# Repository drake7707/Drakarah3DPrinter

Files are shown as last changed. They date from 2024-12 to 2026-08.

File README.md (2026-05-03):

# Drakarah 3D Printer
Everything related to my 3D Printer

**[Blog](/blog.md)**

PXL_20260503_095724243_preview

## Info

The printer started of a Formbot kit and has been upgraded.

The printer is capable of printing multiple colors and multiple materials on a 350x350x340 build volume, except for the volume where the docks reside so it's more 350x250x340 and 350x350x100. It also has a cutter toolhead to cut vinyl sheets.

The build steps for the full kit you can find [here](https://github.com/Zev-se/Formbot-voron-2.4-build-guide)

My build log is on Instagram as reels: [part 1](https://www.instagram.com/stories/highlights/18031423286360519/) and [part 2](https://www.instagram.com/stories/highlights/17904237141050138/)

### Hardware Additions:

 - [Clicky clack door](https://github.com/tanaes/whopping_Voron_mods/tree/main/clickyclacky_door) for better sealing of front door
 - [Tough latches](https://www.printables.com/model/1061047-tough-latches-with-space-for-18mm-dowel-pins) (remixed with 1.8mm dowel pins) for easier panel removal
 - [Beefy Z idlers](https://github.com/clee/VoronBFI) for easier Z belt tensioning
 - [Front USB keystone](https://www.printables.com/model/609433-voron-skirt-keystone-for-usbethernet) to easily plug in an USB stick to print from that when network is not availabe
 - Very cheap USB Camera which I dissected to extract the board, access the focus ring and print my own smaller more [adjustable mount](https://github.com/drake7707/Drakarah3DPrinter/blob/main/CAD/CameraMount.step)
 - USB splitter 1 to 4 to give me extra USB connections, one towards the back keystone panel, one towards the front USB keystone, one for the USB camera and one used by a Wifi adapter
 - Sonoff POW R2 to monitor the power usage of the printer (posts to MQTT)
 - [Handles by 1-0-R](https://mods.vorondesign.com/details/xa84lhUN5aMX4nmfZquaQ) with [spacer](https://www.printables.com/model/1098129-top-hat-spacer-for-voron-handle-by-1-0-r) so I can lift and tilt the printer more easily
 - [Wiper nozzle (Bambu style)](https://www.printables.com/model/1054455-voron-24-nozzle-brush-using-bambu-labs-a1-silicon) which is really important as a non clean nozzle will affect probing and thus Z-offset
 - [Stealthchanger](https://github.com/DraftShift/StealthChanger)
    - Top hat to make room for the umbilicals and retain full enclosure
    - Extra Stealthburner toolheads
    - Fysetc Hexa distro fusion board with backpack for CAN distribution
    - Shuttle instead of TAP
    - [Mini BFI](https://github.com/DraftShift/StealthChanger/tree/main/UserMods/BT123/MiniBFI%20%2B%20MicroBFI) so the gantry clears the crossbar
    - [Docks](https://github.com/DraftShift/ModularDock) with crossbar
    - [N3MI exhaust panel v2](https://github.com/DraftShift/CableManagement/tree/main/UserMods/N3MI-DG/Umbilical_plates_V2) and [Fsyetc hexa distro backpack](https://www.printables.com/model/1366367-fysetc-hexa-distro-fusion-backpack) for CAN cable distribution (and USB hub)
    - [Axiscope](https://github.com/nic335/Axiscope) with hartk sexbolt for easy inter-tool nozzle offset calibration
    - 450W Meanwell power supply to replace the Formbot 200W one to make sure all toolheads can be heated at the same time
  - Vinyl cutter toolhead
  - [The Filter](https://www.printables.com/model/334276-the-filter-for-voron-24) with side bed filters (instead of Nevermore) (the screw-in remix)
  - [Filament rollers](https://www.printables.com/model/73636-filament-spool-roller-w-608-bearings)
  - [FilamAtrix toolheads](https://github.com/thunderkeys/FilamATrix) (ECAS inlet, filament runout sensors and filament cutter integration)
  - Replaced the formbot LED bar with [LED bars](https://aliexpress.com/item/1005003166484007.html) that were easily cuttable to size to improve even lighting and remove shadows
  - [CW2 Filament feeders](https://www.printables.com/model/1709031-clockwork2-filament-feeders), with Fly D5 control board in a [backpack](https://www.printables.com/model/1709021-fly-d5-side-backpack) and [Annex belays](https://www.printables.com/model/1709023-annex-belay-array-mount) to keep extruders in sync
    
My steps to convert to StealthChanger are [here](journey-to-stealthchanger.md)

My steps to add a cutter toolhead are [here](journey-to-stealthcutter.md)

### Software additions
 - Using the latest Armbian image instead of the BTT CB1 image as OS because it gets updates and has the latest kernel (was necessary for wifi adapter drivers) and CPU frequency governor support
 - [Klippain Shake&Tune](https://github.com/Frix-x/klippain-shaketune) (for belt comparison and input shaping)
 - [TMC Autotune](https://github.com/andrewmcgr/klipper_tmc_autotune) with everything set to performance because I had issues with 'silent' tuning
 - Exclude object
 - [Klipper Backup](https://klipperbackup.xyz/) (to automatically backup the config to github)
 - [Crowsnest](https://github.com/mainsail-crew/crowsnest) and [Moonraker Timelapse](https://github.com/mainsail-crew/moonraker-timelapse) (for webcam stream and timelapse gneneration)
 - [NanoMQ](https://nanomq.io/) running as a systemd service as a MQTT server, where a Sonoff pow R2 is posting power metrics to, and moonraker ingests those values
 - [udev-media-automount](https://github.com/Ferk/udev-media-automount) as a systemd service to auto mount USB sticks, a symlink is created to the gcodes folder so USB sticks are exposed on the klipperscreen for printing
 - @reboot script to always create a fixed symlink for the usb webcam, it sometimes was /dev/video0, sometimes /dev/video1 so with a udev rule it is now always /dev/webcam
 - Mainsail [fork](https://github.com/fakcior/mainsail/releases) by fakcior for toolchanging and [toolmapping](https://github.com/fakcior/klipper-toolchanger-tool-mapping)
 
## BOM

I try to keep track of a full bill of materials of the entire printer, so anything I add or remove gets updated in the BOM. You can find that [here](BOM.ods)
<details>
  <summary>BOM overview</summary>
  
</details>

## Lessons learned and things I would change if I did a new build

There are some things that I would do different now that I have built one and ran into several issues over the months

 - Print parts out of ABS instead of eSun ABS+. eSun ABS+ used to be recommended but since they changed their formula layer adhesion and heat resistance is bad.
 - Use an Octopus Pro board with a RPI4 instead of a M8P with CB1 that the Formbot came with. Unfortunately there is no option to choose that when ordering a new kit so I'd be stuck with it anyway, but the CB1 really is not powerful enough. A lot of TTCs and timing issues come down to host delays. It can be mitigated somewhat by using the latest kernel with armbian, setting up a performance CPU governor, adding nice to klipperscreen and other non essential processes and so on but all of this would be avoided if I could just use a RPI4. Being stuck with having to use a compute module for the M8P is really limiting the options for upgradability.
 - Get a bigger 24v power supply, the default 200W that came with the kit is good for a single toolhead, but not so if you run multiple toolheads in a toolchanger. I got away with it with using 3 toolheads of varying sized heaters, 70,60 and 40W but there really is no more room to add another one.
 - Use screw in magnets instead of glueing them in with CA glue. They keep popping out. 2 component epoxy also works and it makes it easier to position the magnet properly as it has a longer setting time but ideally I want something that is more robust.
 - Use 3mm wide spring steel instead of 2 1mm piano wires so the umbilicals don't flex to the side as much. I've changed all the umbilicals and it works so much better.
 - Buy decent fans for the toolheads. The cheap ones are either obnoxiously loud or don't cool the hotend that well. Ideally I want fans with rpm monitoring to stop heating when the fan fails.
 - The EBB36 toolhead board is half the price as a SB2209 and works just as well. The terminal block kind of sucks compared to the molex connector for the heater and there is no easy 5V/12V fan option but the price makes up for it. It's also not limited to just the StealthBurner toolhead.
 - Speaking of toolheads, the stealthburner looks good but there are more lightweight and more compact toolheads available. Anthead is popular for StealthChanger builds.
 - Don't buy a Dragon HF hotend. It's really not worth the extra price when you can buy 4 Bambu like TZ2.0 V6 style hotends for the same price. Even the super cheap V6 clones work well.
 - Buy 10m PTFE tube instead of the cheaper 1m, it's so much nicer to just have enough PTFE tube that bends are relaxed. So many issues I had with underextrusion and PLA filament snapping under stress was due to tight bends or pinched points in the bowden tube.
 - Don't put your printer on a spot that has a lot of sunlight. Yes the free heating is nice, but ABS parts really don't like UV and mine significantly bleached after only a couple of months.
 - Anything that is loose will rattle loudly during printing and annoy you. The Filter lids are slide in lids and not tight enough to not rattle, some superglue fixed that. The Clicky clack door panel also needed some extra panel or it would rattle in its extrusions. Test for rattle during assembly.
 - Pull on your dang crimps after crimping. If they come off it was a bad crimp and can cause intermittent connection issues. I've made some bad crimps and the thermistor dipped and caused prints to fail. Having to disassemble to recrimp is no fun, test during assembly.
 - Don't use cheap USB hubs or usb cables that come with boards. The USB A to C cable I used with the hexaboard caused issues, causing very sporadic lost communication issues (or immediate when heating up all toolheads at the same time). I replaced the cable with a USB3.2 branded one that's likely shielded and much thicker and those issues were fixed.

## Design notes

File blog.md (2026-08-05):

# 2026-08-05 CAN bus instability

A couple of months ago I struggled with lost communication. That hasn't happened anymore (touch wood) but I did still see the bytes invalid, bytes retransmit and CAN RX and TX errors creeping up steadily:


After doing all the CAN cable recrimping I thought I finally had solved it but nope. The screenshot above was while T1 was printing, note how T0 gets bytes_invalid from messages to T1. SB2209s are a pain the ass, don't use them in a stealthchanger. With 2 SB2209s I had to put 3 termination resistors in dropping the resistance between CAN L and CAN H to 48ohms instead of the 60ohms it should be, reducing the margin for noise, with just 2 the second SB2209 just refused to connect. It's been a pain in the ass to get the CAN bus working properly with 2 SB2209s and I suspect a lot of the CAN instability comes from having 2. I don't know what CAN transceiver shenanigans it pulls but I have none of that with the EBB36s.

It used to be fine, but as I added more toolheads and the Fly D5 board the CAN bus gets increasingly chatty, increasingly stubby with more reflections and it caused a lot of issues. With just T0 and T1 the CAN bus was far more stable.

I got so fed up with it, a CAN bus that's unstable can ruin a print several hours in, I didn't want to risk long prints anymore. So I bought an EBB36 and replaced the entire T1 toolhead SB2209 and SB0000 board, similar how T2,T3 and T4 work. I had to do several hours of recrimping, extending wires, creating a new umbilical for T1 (it's a microfit connector and not a 2+2 whatever SB2209 uses). Thankfully I still had everything on hand, had spare cabling and wires and 5 hours later I have exactly the same printer in hopefully a better stable CAN state.

And after printing the toolhead cage for T1 on T1 with the new wiring to test the CAN bus and test T1 stability there are 0 errors, 0 bytes invalid, 0 bytes retransmit for an 90 minutes of printing:



So I can finally call this fixed.

# 2026-05-03 Clockwork 2 filament feeders

The long filament path has been annoying me, I had underextrusion issues from time to time, mostly with ABS and I suspected the nearly 2 meters of PTFE tubes to be the cause, mostly because when they were shorter I never had that issue.

So I decided to make filament feeders. There isn't really a specific project or guide for it so I just chose to make some CW2 with a modded ECAS04 at the bottom. Then I bought a very cheap 5 motor control board, a Fly D5 with cheap TMC2209s to control the motors. Finally I also added Annex Belays to make sure the extruders stay synchronized, so one doesn't starve the other of filament or one doesn't push too much filament.

It took a while because I had to make mounts, covers, print everything, solder everything and make compatible connectors for the board but once everything was assembled it works well.

I tried to do proper cable management because that's 20 wires for the motors, 5+1 wires for the filament sensors in the CW2 (I daisy chained the ground) and 5+1 wires for the belay microswitches. It became a mess of cables quickly so I bought some cable shroud and made some cable clips to route it along the extrusion.

PXL_20260503_085024953_preview

PXL_20260503_085055577_preview

PXL_20260503_084830665_preview

PXL_20260502_183926045_preview

PXL_20260502_184737862_preview

# 2026-05-03 Debugging the occasional lost communication

I haven't really used my 3D printer a lot lately, but when I did print something I had the random "Lost communication with the MCU". Tracing the issue proved tricky with just klippy.log so I imported the mcu and CAN bus stats in home assistant to track bytes_invalid and retransmits and CAN errors over time. I also made a standalone [dashboard](https://github.com/drake7707/klipper-comm-tracking) that you can use. That shed some light on things that shouldn't be there, for example T0 and T1 have slowly increasing bytes_invalid and bytes_retransmit. I'm chalking that down to SB2209s shitty CAN transceivers, that refuse to work with a proper CAN bus and require an extra termination resistor. But I also saw increasing CAN TX errors on the hexaboard and considering that's also the USB to CAN board I suspected the board next or the cables leading up to it.

I could luckily (?) reproduce comms issues when I heated all the toolheads at the same time. The hexaboard errors spike and it loses communication immediately. Interestingly when I disabled crowsnest and thus removed the webcam from the equation it worked. This definitely pointed towards USB cabling issues and not the hexaboard itself, the webcam isn't even connected to the hexaboard but to the M8P. I tried using an USB extension cable routed from the front keystone to the hexaboard and it got way worse, those were cheap usb cable extenders for mice/keyboards so no surprise there.

I luckily also had a decent USB3.2 A to C cable I bought as a spare and it's much thicker while shorter than the cable I used for the hexaboard. I replaced it and things worked fine with the webcam still enabled, no more increasing hexaboard TX errors either. The cable tip is molded bigger so I tried using a 90° USB C to C adapter and that immediately caused the issues to come back. So what I think is happening is that the USB C connector of the hexaboard has too much play with cheaper cables. When I jostled the USB cable I saw the hexaboard disconnect so that was likely the culprit. The USB3.2 cable has a better male connector that connects better so I kept that one, redid the back umbilical with that cable, had to pull out the keystone because it was juuuust too short to reach the electronics bay but hey whatever.

So moral of the story: don't use cheap USB cables, don't use cheap USB hubs, they will work but they will also cause intermittent issues that's not a problem for most devices but for time critical elements it is better not to cheap out. Don't even use the provided USB cables that come with the boards, use known reliable ones and it'll save you a lot of headaches.

I've also bought ferrite chokes but didn't receive them yet. I'll add them to all cables and also all CAN cables to hopefully supress noise from motors and other induction sources, to reduce the CAN errors further. Considering the CAN bus is differential I doubt it's going to matter much but if it drops the noise floor it should help.

While I was in the e-bay (I really did not look forward to flipping the ever increasingly heavy and tall printer) I also cleaned up some wire mess and added an extra fan. I'm running the 24v 6020 fans on 12v and always on at 50% while the printer is on and 100% while the printer is active. Idle they are barely hearable and it keeps airflow going over the CB1 and M8P, which is important because the CB1 comes very close to thermal throttling if fans aren't running + the 450W PSU starts its own very noisy fan when the temperature gets too warm, now it doesn't with the fans providing some airflow.

# 2025-08-05 Finishing up & toolless homing

I've finished building the remaining toolhead and routing all the umbilicals and bowden tubes properly. Even put some numbers on the toolheads and filament inlets to keep track of which one is which

PXL_20250804_173238952_preview

The bowden tubes are slightly less than 2m long, which I hope isn't going to introduce too much friction but it does look a lot nicer and has a lot less bends in it.

PXL_20250727_120601292_preview



I've also spent some time getting toolless homing to work. It looks a lot nicer when all the tools are parked in their docks but the toolchanger software didn't allow for shuttle only homing

Watch the video (https://youtube.com/shorts/G2TRkZCBAtQ)

I had to do a couple of things: 

1. Make a Z-endstop that the shuttle could reach but doesn't interfere when tools are on the shuttle PXL_20250803_063140733_preview

2. Define a [tool_probe] with a negative tool number for the endstop
   
2. Make a small patch in klipper-toolchanger to allow multiple probes not triggered if one of the probes is from a negative probe (because the endstop will always be not triggered)

3. Adjust the homing sequence to check if there is a tool or not and home X,Y then move to the endstop and home Z for shuttle only.

It works fairly well and I can pick up tools without an issue.

# 2025-07-26 Summer upgrades

With the Aliexpress summer sales I bought enough stuff to build a 4th and 5th toolhead. This time around I wanted to build the 4th toolhead as a [FilamAtrix](https://github.com/thunderkeys/FilamATrix) toolhead with cutter and runout sensor built in. 

PXL_20250717_131254119_preview

This ended up not being so straightforward. The v6 mount is not supported by FilamAtrix, so I used the one from Filametrix, but that also meant I had to cut the blade differently (I could not cut the hardened steel blade, instead I bent until it shattered in roughly the correct spot) so it rests on the lip of the heat sink and I had to add a sleeve with PTFE tube and a chamfer cut with an exacto knife. That seemed to work alright. I also had to chafe off part of the extruder housing because the clone V6's stick out 1 mm and it clamped the knife down when assembled so cutting away some plastic gave it some room to cut without any friction.

PXL_20250726_083201591_preview

The filament runout sensors also were not easy to install. The ball bearings are exactly 5.5mm so that wasn't the problem, but the holes in the switches did not line up with the holes to mount them. If I did force screws through they would be too close and be always triggered. I ended up fiddling with it, adding some tape to the front, drilling out a hole on the other so I could get it to the position where it reliably triggered/not triggered when I added/removed filament.

I found the best way was to add some layers of tape on the switch and then screw in the self tapping screws with an angle, that seemed to work very consistently across multiple toolheads.

Another issue I had was I had to add spacers for the Octotap as the extruder motor is a lot taller than the ones I bought previously

PXL_20250719_090806072_preview

It still triggers correctly so not a big deal.

I forgot how long it took to trim wires to length and crimp connectors, but in the end I have a new toolhead.

PXL_20250719_121814919_preview

One of the other things I wanted to tackle at the same time was redoing my umbilicals with spring steel. I used piano wire before and they were very sloppy. So I printed the umbilicals v2 exhaust plate from N3mi, detached everything, removed all the cables, and rebuilt the umbilicals, this time with proper PG7 glands on T0 and T1 too so they screwed in snugly, the ones I had from Formbot had a different pitch or out of spec tolerances and it just didn't sit well in the exhaust plate, that also caused a lot of sloppiness.

PXL_20250723_124743320_preview

Pretty happy with that, they look a lot better and hold their form a lot better.

I also managed to snag a Fsyetc Hexa Distro Fusion board for an early bird deal, it's a distribution board for both CAN and USB toolheads but also has a dedicated chip with lots of GPIO. That means I can add a lot more sensors directly to that board instead of having to route everything to the electronics bay.

PXL_20250724_132922123_preview

It's a very new board and there isn't a proper mount for it yet, so I took the time to redesign a new backpack to hold it in place.

PXL_20250726_152013076_preview

One of the other issues I had was filament breaking in the bowden tubes at certain points because the filament was under stress, especially the cheap PLA is very prone to that, so I really want to reroute the bowden tubes to have as little sharp bends as possible, I bought 10m so I can cut them to length and use 2m instead of 1m to make a gentle path towards the spools.

It's still a work in progress in the end the printer will be a lot better, it's the small things.

# 2025-07-10 Sun exposure

I put my printer in my office room on a spot that received a lot of sunlight. I thought the free heating for the chamber would be nice, but now that it's summer the UV is a lot higher and my ABS parts are suffering, I didn't realize how much they have become bleached until I printed a new part and held it next to an older part.

PXL_20250710_134234707_preview

Yikes. Needless to say I moved some things around.

# 2025-06-29 Axiscope

After the last recalibration I ordered the parts to try out Axiscope, basically aligning the tool nozzles visually with a camera. It was pretty cheap anyway, cheaper than a sexball probe and it works great. I had to solder 4 leds (I ordered leds that were too large so I had to drill the holes bigger) to the board, snapped it shut, glued in 2 magnets (4 really seemed overkill with N52) and it works well. The webpage to control the toolhead and measure the offset is pretty easy to use and I could do an entire calibration in a few minutes or less, much faster than the shenanigans I had with the sexball probe and probe that used a StealthChanger pin and bushing, no more going out of bounds, no more samples exceed tolerance, just align and bam done. My calibration was pretty spot on, they were already pretty well aligned, which meant that the values I got from the probe were not very accurate because that suggested over a mm change.

Pretty happy with it, now I just need to change the sexball probe into a normal Z-endstop and set up Axiscope to use the probe for calibrating the Z-offsets.

PXL_20250629_163239899_preview

If you're unsure which tool calibration method to use, I heartily recommend this one.

Another thing I learned recently thanks to https://youtu.be/mkgGAVH_XZM is why my sexball probe and pin probe were so inaccurate no matter what I tried. I thought it was the tolerance of the pin and bushing but I never considered the concentricity of the nozzle orifice. I run very cheap nozzles so I doubt they are symmetrical and concentric at all, giving me a bias towards one side. Another reason why camera based alignment is so much better and easier, it takes out the guessing game of whether tolerances are good enough and doesn't rely on the quality of parts.

# 2025-06-10 Recalibration & print

I managed to recalibrate the nozzles, my sexball probe is useless, it was way off, there's just too much play in the sexball probe shaft and bushing so I need to find a better way for calibration, I might try [Axiscope](https://github.com/nic335/Axiscope), which would be great for X,Y alignment and rather cheap. Z I can do easily with a test print. Anyway, after multiple test prints I got it dialed in properly.

So I did a stress test print and the second attempt worked fine (I had some issues with my config of Tool mapping that nuked the first attempt):



It came out nicely, I scaled up Calidragon by 200% so it was 352 tool changes and it worked flawlessly. It took 4h23min, mostly because my tool changes weren't super optimized to be fast.

So I did that next, increased the Z speed to 200mm/s from 150mm/s, increased Z acceleration to 750mm/s² from 350mm/s². Optimized the pickup and dropoff gcode to use faster XY speeds (300mm/s), removed the M400 from the dropoff gcode that introduced a delay and removed the verify code on pickup as it gets verified after the pickup code runs anyway, it was there to bail out early before potentially dragging the tool off the dock. Bit of a risk but my tools have survived the dive to the bed before.

And i've gotten it down to about 8 seconds for a tool change, it used to be around 15 seconds:

Watch the video (https://youtu.be/LBZMbHjzhpM)

It's really nice to see such a big improvement over my past multi color prints.

# 2025-06-08 Software updates and shenanigans

I was still on the klipper-toolchanger commit from July 2024 and some improvements had been done recently to not have those false positive crash detection triggers anymore, I couldn't also update Klipper because the old version wouldn't be compatible so I took the plunge and updated everything.

Unfortunately a lot had changed since in the gcode as well and nothing was documented, so I had to compare my gcode for picking up and dropping off tools with the newer version. Eventually I got it working, mostly.

One issue I encountered was that the now split dropoff and pickup path was not correct for my Stealthchanger and Stealthburner tool heads, so I used the old path. That worked but not before ramming T0 at full speed into the bottom of the docks.

This has unfortunately some consequences, or maybe it had to do with the update, I don't know, but T0 and T1 would not dock properly anymore. I had to recalibrate the dock and park position of the tools so it drops it nicely without moving and can pick it up without any jerkiness to the pins. This is really important because it would lead to sporadic docking/undocking issues.

After that I noticed when starting a print that the crash protection now works differently and I had to put it a verify tool check in the after later gcode. I don't like this, this causes a delay on every layer change, so I will probably remove that check. Most if not all crashes happen during tool changing anyway.

When I finally gotten a multi tool test  print done again I noticed my calibration was way waaay off, especially on T1. I did remove the nozzle and hotend at some point after a jam and didn't recalibrate.

So I recalibrated, and then the magnet in the shuttle decided to come loose, as well with several pins from T0 due to the added friction of not having a magnet snap the tool in place. Sigh, this would have been a good time to use the two component epoxy I borrowed but apparently lost when I forgot to close the zipper of my bag. I ordered some from Amazon to replace that, but that meant I had to use super glue *again*, which means it will fail again in the near future.

Getting the stupid magnet to sit flush in the shuttle is a pain when there's superflue underneath it. I seemed to have raised it a wee bit because T0 now had inconsistent probe trigger issues. It really never stops does it? Anyway, it was only T0, the others were fine, I loosened the Octotap, pushed it down as far as I could and tightened it again and that did the trick. I already did that on the other tools so I knew it was a good thing to try.

So now I just have to calibrate the z-offset and gcode offset of every tool again, the new magnet location will have shifted things somewhat and then it should be good to go.

I really want to do another multicolor print in a hopefully more reliable fashion but this ended up being a whole lot more work than I planned for.

# 2025-05-15 Some small updates

I've done some small software updates, mainly for some quality of life:

1. I've switched mainsail to the [fork](https://github.com/fakcior/mainsail) with toolchanger support by fakcior. This gives me a nice UI box per tool to activate,load and unload the filament. I could already do that on KlipperScreen but it's still kind of a hassle. Tool remapping is another big one, there is currently no way in OrcaSlicer to swap colors in a painted m3f model, which means I would need to swap the filaments to the tools according to the painted scheme. That's kind of dumb, luckily [this](https://github.com/fakcior/klipper-toolchanger-tool-mapping) allows for remapping the gcode before starting the print. It's still an extra step but at least it's possible now
431562327-bf8e2c3a-cb0d-4ef9-af06-b4f71f41f3fb (*screenshot from the repo*)

2. I've changed some macro's here and there, nothing major, things like not disabling the motors on print end and moving to the nozzle brush before heating up to target temp so the ooze doesn't get dragged all over the bed.

3. The filament rollers work pretty well, but sometimes it does snag hard enough on the roll that it yanks it off the roller sideways, I have added some filament guides to hopefully mitigate that

# 2025-05-06 Vinyl stickers are cool



I used the cutter to make some decals for the top hat, the small lettering was a pain in the ass to transfer but I got it in the end, kinda.

# 2025-05-06 Filament spools driving me crazy

The stealthchanger backpack I made really did not have great routing of the PTFE tubes, my printer is in the corner of my room and accessing the filament spools on the far side was a nightmare, I actually bent the PTFE tube multiple times, there was also no strain relief. The shitty Sunlu PLA+ filament breaks if there is so much as a tiny bit of resistance if it's not dried which also prompted this change.

I got so pissed off I changed the whole thing, initially I designed a spacer to hold the PFTE connectors but that didn't work because the bent upwards would be too great, so option B, drill holes in the backplate of the backpack and use raw force to thread the connectors in. It's not pretty and I really should reprint the back plate with proper m10 threaded holes, but it will do for now.



It makes removing the back plate harder and putting it back in place against the barbs of the connectors even more so (luckily I can push the black rings around it down to keep the barbs from biting into the PFTE tube, one at a time)



Next, filament rollers:

I used [this](https://www.printables.com/model/73636-filament-spool-roller-w-608-bearings) model, bought some 608 bearings, realized I needed 20 not 10, so I printed [some 608 bearings](https://www.printables.com/model/561588-bearings-print-in-place-with-real-rolling-elements), they have more resistance but they work.

I extended the rail to the full size of the top, and then cut it in the slicer with a dovetail cut, that didn't work on such a tiny surface, should have just made a slot on one end and screwed it down, but some electrical tape holds it together.

I designed a [clamp](https://www.printables.com/model/1287401-filament-spool-holder-rail-clamp) to bolt the rail to the side extrusions, similar to the top panel clamps, which makes it sit snugly against the top panel. Together with the weight of all the rollers there is almost no play in the rail.



# 2025-05-04 Cleaning up the rat's nest of wires

One thing that was on my TODO list and I was very reluctant to do was to move the Sonoff Pow R2 from an external extension cord to internal. I was reluctant to because I don't like messing with AC wires, but I finally did it anyway. I quadruple checked all the crimps, using the different crimp clamps on my crimper to make sure the wires are in securely (some weren't so good thing I checked!), then cut some wiring and went to work. Finally I stuck the Sonoff on the bottom plate with some double sided tape.



Everything still works, nothing blew up and it's a lot cleaner behind my printer now.

# 2025-04-28 Cutting edge technology

I finally got a cutter, details are [here](/journey-to-stealthcutter.md)

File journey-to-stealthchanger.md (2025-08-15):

# Journey to stealthchanger

## What

[Stealthchanger](https://github.com/DraftShift/StealthChanger) is a toolchanger so multiple tools can be used in the printer. This is significantly faster than multimaterial that uses filament retract and spool rewinds to feed in new filament.

It requires a fairly large amount of modifications (with multiple options) so I thought it'd be nice to write down the ones I did and what my experience was with them.

## Why

It looks cool and it gives me a spare toolhead. I already had a V6 nozzle that I didn't use that came with the kit because I bought the Dragon HF hotend. Being able to print multiple colors way faster than a filament respooler such as ERCF or Box Turtle + having a lot less waste (some colors such as black -> pink really bleed badly into each other needing a lot of purged filament) was a nice bonus. 

## Step by step

### 1. Second toolhead

Building a new toolhead is pretty much the same as building the first toolhead. This time I had to crimp the wires myself instead of using the provided wire loom but it was pretty straight forward. I stuck with what I already knew and bought a SB2209 (RP2040) CAN board with the same MOONS NEMA 14 extruder).
.

I did buy some shitty fans mostly because I wanted to keep costs down and I didn't know if it would work well. I probably will upgrade to better fans later.

### 2. Docks

I printed and assembled the modular docks from DraftShift Design (the same team behind StealthChanger). Assembling them is pretty straight forward, building the cup filled with RTV silicone was the most annoying and messy part. The wiper to hold the small PTFE tube kept breaking too, but with some superglue and some old laptop screws I managed to get it built.





When mounting them from the top frame it was pretty evident that it wasn't very stable. With the filament I used they vibrated and flexed around a lot, even with torsion so they weren't fully straight. Trying to fix that with the bolts did not work well, so I ended up adding a crossbar.

There are a couple of options to provide bottom support, a crossbar with a doorbuffer is the easiest, it spaces out the support in front of the frame providing clearance for the gantry idlers. I instead already bought some 2020 extrusions for the top hat to size, so I used a crossbar between the vertical frame. That also meant ripping out the default front idlers and replacing them with [Mini BFI](https://github.com/DraftShift/StealthChanger/tree/main/UserMods/BT123/MiniBFI%20%2B%20MicroBFI) that don't portrude past the frame extrusions



I ended up redoing the docks removing the top support with [Crabby docks](https://www.printables.com/model/994635-stealthchanger-stealthburner-minimal-docks-aka-hap). It looks nicer and doesn't obscure as much


Rather than using magnets to lock the tools in I'm using screws with PTFE tube over them. That secures the tools so much in their docks I can put the whole printer on its side and they will stay put. I tried with 5x2mm magnets but they were not powerful enough to keep the tool in place and it limits the tilt enough that I could reduce the umbilical length, which in turn helped with umbilicals not getting stuck under each other



### 3. Sensorless homing

When installing the shuttle there is no X-endstop like there is on the TAP carriage (because otherwise tools wouldn't be able to be detached), so the easiest option is sensorless for X (I ended up doing sensorless for both X and Y). I followed [this](https://github.com/EricZimmerman/VoronTools/blob/main/Sensorless.md) guide and it worked fairly well. The gotcha that got me was that I had to configure TMC autotune as well, otherwise it would work while calibration but fail during normal operation. And it is quite scary home incorrectly and then have the toolhead slam into the gantry. Make sure you calibrate when the gantry isn't level, it adds extra friction so your threshold isn't triggered too soon. 

After installing the shuttle, the belt ends were hindering X homing (and also replacing the umbilicals with stiffer ones) I had to lower the threshold for Stallguard a bit, or it would trigger prematurely so this might need tweaking in the future.

### 4. Faster Z movement

By default the speed is 15mm/s, that is pretty slow to do a tool change. I gradually upped the speed but could not get past 50mm/s. Thinking it was a hardware issue, I checked all the Z-drives grub screws, checked and tensioned all the motor mounts so there is no slack on the big pulley when the motor is initialized (so no backlash), upgraded to [beefy Z idlers (BZI)](https://github.com/clee/VoronBFI/tree/main) and retensioned the belts, but the problem remained. It turned out to be TMC Autotune that put the Z motors in StealthChop and that doesn't work well with higher speeds. Disabling TMC autotune or setting the tuning to performance fixed the issue and I am now running at 100mm/s without a hitch, probably can push it even faster.

### 5. Shuttle

The TAP carriage needs to be replaced with the StealthChanger shuttle. In fact if you put a backplate on a tool and the shuttle on the X rail then everything will still work with the TAP configuration. I ran this for quite some time, this is how I gradually converted my printer to Stealthchanger without losing the ability to print while doing so.

I struggled here to print the shuttle belt grooves properly, so I ended up using the shuttle keeper spacer to hold the belts in place and then bolt the shuttle to the keeper and the carriage.

Finding N52 magnets seemed to be hard, I found some on amazon but they were 6.7mm diameter instead of 6mm, which meant I had to make changes to the holes where they are inserted. At this point I've gone through several destroyed shuttles and backplates so this got delayed a lot. I ended up buying N52 magnets from Lecktor and those were 6mm.







With the help of the belt keeper I tensioned the belts so I didn't even have to use the idlers tension screws much.

I didn't have any issue mating the shuttle with the backplate, I first installed the bushings in the shuttle and glued them in place. I cracked several shuttles trying to insert the bushings (don't use eSun ABS+ for a shuttle). One shuttle ended up cracking when I bolted it to the carriage, which caused the bushings to have too much play and not trigger the Octotap sensor anymore.

My octotap sensors combined with my printed shuttles are very sensitive to slight deviations in angle, so while I initially just extended the shuttle tip by gluing a piece of filament on top so it triggers octotap more reliably it was really solving a problem whose cause would have other issues as well. So my latest attempt that seems to work well is:

 - Install bushings in shuttle, glue them in place so they can't move around and flex
 - Install magnets in the shuttle. Make sure to fit them in first before adding glue because mine set too quickly and caused one of the magnets to not fully seat *sigh*. Tolerances 🙄
 - Mate with a backplate so the pins are aligned to the bushings, glue the pins in place and let it dry while mated with the shuttle, that ensures they stay aligned
 - Add the magnet in the backplate, make sure of the correct polarity, glue it in place after fitting them first
 - Add and adjust the preload screws of the backplate, first screwing them fully in and then back them out by half or quarter turns each. Too far and the octotap won't trigger anymore, not far enough and there will be too much play. When putting the toolhead on the shuttle there should be absolutely no side to side play (rotation around the Y axis), if there is probe accuracy will suffer. Adjust the preload screws until there is none.

Those N52 magnets are strong, make sure to use enough glue, I didn't at first and they got loose after a while causing probe accuracy issues and eventually tool changes to fail. I also had my nozzles dragging over the print during fast travel moves.

After doing that I have good probe accuracy and no issue with tool changes.

In fact to troubleshoot probe accuracy I now check:
 - Loose screws anywhere? Shuttle screws, backplate screws, octotap screws?
 - Are the magnets still sitting flush? Are they loose in either shuttle or backplate?
 - Is there play in the toolhead? Check preload screws and adjust
 - Is there wiggle room in the bushings or pins of the backplate?
 - Are there any cracks in the shuttle, especially near the top bushings. Again really don't use eSun ABS+, layer adhesion is horrible.
 - Are the bushings still securely glued in place?
 - Check for warpage of the hotend/backplate, shim if necessary so the nozzle is perpendicular to the bed
 (this isn't very straight anymore :|)

Any of these things will cause probe accuracy, z-offset inaccuracies and potential docking issues.

*Update April 2025* After some weeks of printing it becare clear that CA superglue is *not* good enough to keep the magnets in place, I've had several failures of both backplates and shuttle where the magnet popped out and then rode along so it couldn't tool change anymore. I've been recommended to use 2 component epoxy glue to secure them or use [6x3 with 2mm ID screw in magnets with M2 self tapping screws](https://discord.com/channels/1226846451028725821/1226846451594821707/1359884602902052894) to secure them into the plastic.

### 6. Top hat

Umbilicals are probably the most important in a StealthChanger build. They need to push the tools into the docks so they sit straight (and they can be picked up well) and don't get yanked off by the weight of the umbilical. In order to have enough clearance for the umbilicals the Z needs to be extended. With the top panel in place on the frame it's impossible to reach the full Z without squishing the umbilical so the solution is a top hat.

I wanted to keep ABS and ASA as options so keeping the printing enclosed was mandatory.

There are several options, from a printed top hat to using extrusions and polycarbonate panels. For a 350 build it's recommended to have at least 20mm extra in height, which would be a lot of plastic. I switched to a Clicky Clack door earlier so I had the 2 spare 24cm stock doors lying around, so I decided to go with the latter option.

I miscalculated the vertical extrusion length (I ordered 25cm, and received 24cm for some reason), so my vertical height was off to mount the panels in the same way with tough latches as on the frame panels. I created [a spacer](CAD/TopHatSpacer_v2.step) that not only holds the extrusions together but provides extra height so the 24cm panels can sit flush with the bottom.

My extrusions inner diameter are 5mm, while the ones I ordered from the top hat are 6mm. This is annoying as I was planning to use some M5 dowel pins. I ended up designing and printing them instead, [dowelpin](CAD/dowelpin.step), but the top hat extrusions chafe away at them so they are only good for a limited amount of top hat removals before they break.

Another issue I had was that the handles I was using interfere with the top hat panels, I designed and created a [spacer](Voron-1-R-Handle-Spacer.step) for that too. I designed it in such a way that it could be printed standing on its side to provide the best tensile strength.



Not having an extrusion for the front of the top hat (it's used as crossbar) is a bit annoying to have a tight seal, but the weatherseal strip seems to work alright. Unfortunately my panels were not cut to 0.1mm tolerances, like 0.5mm too tall, which is giving me issues to put panel clamps on the top. I've instead added more on the side to increase friction so it stays put.

Unfortunately it didn't do much for keeping the chamber temperature high for ABS printing, I barely get above 40° C and that's with The Filter + side filters (4 blower fans) at full blast.

### 7. Umbilicals and CAN wiring

*Update: I have redone the umbical wiring with spring steel (a lot better than piano wire) as well as routing of the PTFE tubes and used a distribution board with a different backpack, read about it [here](https://github.com/drake7707/Drakarah3DPrinter/blob/main/blog.md#2025-07-26-summer-upgrades). I'll leave the old write up below but be aware it's not up to date anymore.*

For the actual umbilicals I bought some 1mm spring steel piano wire and used 2 of them next to the CAN cable to provide enough rigidity. A 3mm spring steel strip is recommended nowadays but I didn't have that so I tried to mimic it as best as I could. I used some tape to hold them in place and used some sleeving over it. The first umbilical I didn't put the piano wire all the way to the toolhead and I feel that was a mistake, it bent and pushed the toolhead backwards on the dock. When I extended the piano wire all the way to the toolhead (I use PUG instead of PG7) that worked much better for staying in the docks.

One thing I had to make sure was that the natural curl the piano wires wanted to make aligned with the arc that I wanted the umbilical to make, so i had to clamp them down at the toolhead in the PUG in exactly the right orientation and the same at the PG7 gland at the exhaust.

I used the [umbilical exhaust by N3MI](https://github.com/DraftShift/CableManagement/tree/main/UserMods/N3MI-DG/Umbilical_Plates) to attach the exhausts at the back. I had a lot of trouble getting the PG7 glands to screw in. I initially thought I probably need to tune shrinkage and hole compensation settings more but after buying some new PG7 glands those fit perfectly, so the ones I got with the Formbot kit were out of spec.

Determining the length of the umbilical was not that easy. The docks in the corners need a slightly longer one to make the same arc. Mine are about 70cm but I feel that's still too long. It's a lot of testing that the toolhead doesn't get yanked backwards but also that the front corners can be reached without putting too much strain on the umbilical.

After some tweaking 60cm is a better length, with a longer length they often got stuck underneath each other and they tended to flop more to the side, with 60cm they don't interfere with each other anymore even though they pull the tool backwards more but the tilt is limited by having the physical screws on the docks to lock the tools in place. Too much tilt would prevent correct alignment of the backplate pins with the shuttle so those docks screws are very mandatory with a shorter umbilical.



Then I clipped the reverse bowden tube alongside the umbilicals with some custom designed [cable clips](CableClip-Body001.step) (sized to my umbilical thickness)

.

Finally the CAN wiring. Initially I had the CAN cable broken out in the electronics bay and used some wago clips, but that meant I also had to run each umbilical downwards, that's not very scalable with more toolheads, so I moved the wagos up near the exhaust and ran 2 1.5mm² power wires along with some leftover CAN cable for the CAN wires, all sleeved together and then attached the umbilicals there.



I've designed [a box](https://www.printables.com/model/1119606-wago-can-distribution-box-for-n3mi-umbilical-plate) to make it neater.





### 8. Configuration

#### Installation 

So far installation and configuration is pretty straight forward, I already defined toolheads in seperate config files, so following the [guide](https://github.com/DraftShift/StealthChanger/wiki/Configuration) was relatively easy. Make sure to use the [easy config](https://github.com/jwellman80/klipper-toolchanger-easy) by @averen or use the klipper-toolchanger from June 2024 because newer commits have broken stealthchanger. There is a DSD fork in the works that will bring everything together but right now it's still in alpha and I have not used it yet.

#### Calibration

One gotcha I had during [dock position calibration](https://github.com/DraftShift/StealthChanger/wiki/Calibration) was that (as of the time of writing) it's still recommended to home, QGL and home again with T0, and then find the positions of the docks (this is not mentioned in the guide). The moment I took T0 off the shuttle the crash protection triggered disabling the motors so it was impossible to try and pick up a tool manually to find its dock position. Running `STOP_TOOL_PROBE_CRASH_DETECTION` is necessary to prevent this. Also when picking up the other tool manually, before testing the docking path make sure you re-run `INITIALIZE_TOOLCHANGER` because otherwise it will think T0 is still active and will try to dock on T0 instead of the correct dock (as I found out the hard way).

For the cups filled with RTV the spring on one was too weak causing it to not contact the nozzle. I added a few washers so it sits higher and that seemed to help but it tilts the toolhead backwards. I've added some M3x12 screws in the docks that correspond to the holes of the M3x50mm screws of the StealthBurner toolhead to prevent to lock it in place. It still tilts back a bit but it can't because the screws are holding it back further. That seemed to work fine. Normally you would add screws the other way and use 5x2mm magnets to lock it in place, but I don't have magnetic screws at the moment. I set it up in the following order: 1) put the tool on the dock 2) adjust the cup height so the nozzle hits the RTV of the cup but not too much it causes too much tilt 3) adjust the back of the dock so the toolhead sits level and doesn't tilt to one side other than backwards 4) do a manual pick up and release with the shuttle and adjust until the toolhead doesn't stray too far off so the pins still go smoothly into the bushings once you pick it up again.

For the Z-offset I initially set up both toolheads, but T1 z-offset is never used (T0 is the reference for homing and every position is based on that). I copied over the z-offset I had before with TAP changer and it worked straight away.

I used a sexball probe which wasn't straight forward to get working. There is quite some play on the shaft so I questioned the accuracy. I had to increase the sample tolerance setting a lot to have it finish. I also ran out of bounds several times as the probe is at the fringe of where the toolhead can be. I had to move the bed backwards a bit so the sexball probe testing range was within bounds. At the same time I also moved the nozzle wiper to the front because that couldn't be reached anymore. So what was a simple crimp wire, mount to extrusion, done turned out to be more of an ordeal. In the end I ran it several times and used the offsets that occurred the most. After test printing that also seemed to be the correct offset.

#### Slicer setup

I use OrcaSlicer and as of v2.2.0 it supports multiple toolheads. Unfortunately I had to set up a whole new printer profile from the Generic Multitool profile to do so (and re-apply all my settings). I've set the idle temp in the filament settings and preheat time in the ooze prevention settings so it drops the temperature when not in use (saving power and squeezing slightly more margin out of the 200W PSU). To ramp them up to idle at the start I specified those temperaturates along in PRINT_START. Replace M104 with M109 to do them one by one if the PSU is not strong enough.

This is the machine G-Code from OrcaSlicer (credits go to @theaninova on discord):
```
PRINT_START TOOL_TEMP={first_layer_temperature[initial_tool]} {if is_extruder_used[0]}T0_TEMP={first_layer_temperature[0]} T0_IDLE_TEMP={(idle_temperature[0] == 0 ? (first_layer_temperature[0] + standby_temperature_delta) : (idle_temperature[0]))}{endif} {if is_extruder_used[1]}T1_TEMP={first_layer_temperature[1]} T1_IDLE_TEMP={(idle_temperature[1] == 0 ? (first_layer_temperature[1] + standby_temperature_delta) : (idle_temperature[1]))}{endif} {if is_extruder_used[2]}T2_TEMP={first_layer_temperature[2]} T2_IDLE_TEMP={(idle_temperature[2] == 0 ? (first_layer_temperature[2] + standby_temperature_delta) : (idle_temperature[2]))}{endif} {if is_extruder_used[3]}T3_TEMP={first_layer_temperature[3]} T3_IDLE_TEMP={(idle_temperature[3] == 0 ? (first_layer_temperature[3] + standby_temperature_delta) : (idle_temperature[3]))}{endif} {if is_extruder_used[4]}T4_TEMP={first_layer_temperature[4]} T4_IDLE_TEMP={(idle_temperature[4] == 0 ? (first_layer_temperature[4] + standby_temperature_delta) : (idle_temperature[4]))}{endif} {if is_extruder_used[5]}T5_TEMP={first_layer_temperature[5]} T5_IDLE_TEMP={(idle_temperature[5] == 0 ? (first_layer_temperature[5] + standby_temperature_delta) : (idle_temperature[5]))}{endif} BED_TEMP=[first_layer_bed_temperature] TOOL=[initial_tool] CHAMBER_TEMP=[chamber_temperature] FILAMENT=[filament_type]
```

And this is my print start:
```gcode
[gcode_macro PRINT_START]
variable_printing: False
variable_tools_used_during_print: []
gcode:
  {% set material = params.FILAMENT|default('PLA')|string %} ; Get material type from params
  {% set bedtemp = params.BED_TEMP|default('0')|string %} ; Get the bed temperature
  {% set chambertemp = params.CHAMBER_TEMP|default('0')|string %} ; Get the chamber temperature
  
  M117 Initializing  
  SET_GCODE_VARIABLE MACRO=PRINT_START VARIABLE=printing VALUE=False

  # Register the tools used during print
  {% set tools_used_during_print = [] %}
  {% for tool_nr in printer.toolchanger.tool_numbers %}
    {% set tooltemp_param = 'T' ~ tool_nr|string ~ '_TEMP' %}
    {% if tooltemp_param in params %}
      {% set _ = tools_used_during_print.append(tool_nr) %}
      SET_GCODE_VARIABLE macro=PRINT_START variable=tools_used_during_print value="{tools_used_during_print}"
    {% endif %}
  {% endfor %}
  RESPOND TYPE='echo' MSG="The print uses the following tools: {tools_used_during_print|join(' ')}. M104 will be ignored for all other tools while the print is active"

  INITIALIZE_TOOLCHANGER
  CHECK_ACTIVE_T0 ; Check T0 is active
  
  SET_DISPLAY_TEXT MSG="Heating the bed to target temperature"
  M190 S{bedtemp} ; heat the bed

  SET_DISPLAY_TEXT MSG="Heating T0 hotend to 150c" 
  M109 S150 ; heat the nozzle
    
  SET_DISPLAY_TEXT MSG="Homing" 
  STATUS_HOMING
  G28
  
  SET_DISPLAY_TEXT MSG="Cleaning nozzle" 
  STATUS_CLEANING
  CLEAN_NOZZLE

  SET_DISPLAY_TEXT MSG="Quad Gantry Leveling" 
  STATUS_LEVELING
  QUAD_GANTRY_LEVEL

  SET_DISPLAY_TEXT MSG="Homing" 
  STATUS_HOMING
  G28

  SET_DISPLAY_TEXT MSG="Building adaptive bed mesh" 
  STATUS_MESHING
  BED_MESH_CALIBRATE ADAPTIVE=1             ; do a bed mesh
  G1 Z20 F3000                   ; move nozzle away from bed
    
  M109 S0 # Stop to heat, the actual printing may happen with a different hotend.

  SET_DISPLAY_TEXT MSG="Heating up the hotends to idle temp"
  # Preheat all the hotends in use
  {% for tool_nr in printer.toolchanger.tool_numbers %}
    {% set tooltemp_param = 'T' ~ tool_nr|string ~ '_IDLE_TEMP' %}
    {% if tooltemp_param in params %}
      M104 T{tool_nr} S{params[tooltemp_param]}
    {% endif %}
  {% endfor %}

  SET_DISPLAY_TEXT MSG="Switching to active tool" 
  {% if params.TOOL is defined %}
    T{params.TOOL}
  {% endif %}

  SET_DISPLAY_TEXT MSG="Heating hotend to target temp" 
  M109 S{ params.TOOL_TEMP }
  G0 Z2 F300 ;Move up a bit
  G92 E0 ; Zero extruder
  
  START_TOOL_PROBE_CRASH_DETECTION
  SET_GCODE_VARIABLE MACRO=PRINT_START VARIABLE=printing VALUE=True
  
  SET_DISPLAY_TEXT MSG="Cleaning nozzle ooze" 
  STATUS_CLEANING
  CLEAN_NOZZLE ; clean the nozzle to remove and leftover ooze
    
  SET_MATERIAL MATERIAL={material} ; setup the things specific for the material
    
  SET_DISPLAY_TEXT MSG="Printing" 
  STATUS_PRINTING  
  
#####################################
##            Set Material         ##
##      Version 1.0  2023-4-2      ##
#####################################
## From: https://github.com/rootiest/zippy-klipper_config
## Set Material-specific Configs
## 
## Add this immediately after your start_print line of the start gcode in Prusa/SuperSlicer:
##     SET_MATERIAL MATERIAL='{filament_type[initial_extruder]}'
## 
## Add this immediately after your start_print line of the start gcode in Cura:
##     SET_MATERIAL MATERIAL='{material_type}'
## 
[gcode_macro SET_MATERIAL]
description: Set values based on material type
variable_material: ''
gcode:
    {% set material = params.MATERIAL|default('PLA')|string %} ; Get material type from slicer
    {% if material == 'PLA' %} ; If material type is PLA
        SET_FAN_SPEED FAN=nevermore_fan SPEED=0.0
    {% elif material == 'ABS' %} ; If material type is ABS
        SET_FAN_SPEED FAN=nevermore_fan SPEED=1.0
    {% elif material == 'ASA' %} ; If material type is ASA
        SET_FAN_SPEED FAN=nevermore_fan SPEED=1.0
    {%else %} ; If any other material type
        SET_FAN_SPEED FAN=nevermore_fan SPEED=0.0
    {% endif %}
```

I had the pressure advance settings per filament in the SET_MATERIAL, but I moved that to the filament settings in OrcaSlicer because it emits a SET_PRESSURE_ADVANCE at every filament change.

To make sure T0 is active I used the following gcode. Using any other tool to home and QGL is going to cause issues with z-offset and docking:
```
[gcode_macro CHECK_ACTIVE_T0]
gcode:
  {% set tool = printer[printer.toolchanger.tool].tool_number %}
  {% if tool != 0 %}
    {% set msg = 'T0 is not active, active tool is ' ~ tool|string ~ '. Cancelling print.' %}
    SET_DISPLAY_TEXT MSG="{msg}"
    RESPOND TYPE=error MSG="{msg}"
    CANCEL_PRINT
  {% endif %}
```

One issue I had was that it took a long time for the temperature to settle, even with long preheat time it often caused delays at tool swaps. OrcaSlicer emits M109 at every filament change when using ooze prevention, the default M109 waits until it's stable within 0.5 degrees which is too precise.
There is already an override from TAP changer, but this override from DSD is better as it allows you to set the deadband, so rather than a 0.5° it now uses a 3° variance for stability. This still needs to be tweaked depending on the hotend. My Dragon HF stabilizes much quicker than the cheap V6 nozzle.
```

[gcode_macro M109]
rename_existing: M109.1
description: [T<index>] [S<temperature>] [D<Deadband>]
  Set tool temperature and wait.
  T= Tool number [optional]. If this parameter is not provided, the current tool is used.
  S= Target temperature
  D= Dead-band, allows the temperature variance +/- the deadband
variable_default_deadband: 6.0
gcode:
    {% set s = params.S|float %}
    {% set deadband = default_deadband|float %}
    {% if params.D is defined %}
        {% set deadband = params.D|float %}
    {% endif %}
    {% set tn = params.T|default(printer.tool_probe_endstop.active_tool_number)|int %}
    {% set tool = printer.toolchanger.tool_names[tn]|default('') %}
    {% set extruder = printer[tool].extruder %}

    SET_HEATER_TEMPERATURE HEATER={extruder} TARGET={s}
    {% if s > 0 %}
        TEMPERATURE_WAIT SENSOR={extruder} MINIMUM={s-(deadband/2)} MAXIMUM={s+(deadband/2)}   ; Wait for hotend temp (within D degrees)
    {% endif %}
```
#### Workaround for an annoying [bug](https://github.com/SoftFever/OrcaSlicer/issues/7842) in OrcaSlicer 2.2.0

*Note: OrcaSlicer 2.3.0 is out where this is fixed so this is now not necessary anymore*

When printing single color on any toolhead other than T0, it still preheats T0 for some reason, and it does so multiple times so just setting it to 0° does not work for long. I worked around that by keeping track of the tools that are used in PRINT_START (see '#Register the tools used during print' above) and then check if the M104 call to heat a toolhead is in that list:
```gcode
[gcode_macro M104]
rename_existing: M104.1
description: [T<index>] [S<temperature>]
  Set tool temperature.
  T= Tool number, optional. If this parameter is not provided, the current tool is used.
  S= Target temperature
gcode:
  {% if params.T is defined %}

     {% set can_change_temp = False %}
     {% if printer["gcode_macro PRINT_START"].printing %}
      {% set tool_nr = params.T|default(printer.tool_probe_endstop.active_tool_number)|int %}
      {% set tools_used = printer["gcode_macro PRINT_START"].tools_used_during_print %}
      
      {% if tool_nr in tools_used %}
        #RESPOND TYPE=echo MSG="Tool {tool_nr} is used in print, can set temp to requested tool"  
        {% set can_change_temp = True %}
      {% else %}
        RESPOND TYPE=echo MSG="Tool {tool_nr} is not used in print, ignoring request for M104"
      {% endif %}
    {% else %}
      #RESPOND TYPE=echo MSG="Not printing, can set temp to requested tool {tool_nr}"
      {% set can_change_temp = True %}
    {% endif %}

    {% if can_change_temp %}
      {% set newparameters = "" %}
      {% set newparameters = newparameters ~ " T="~params.T %}
      {% if params.S is defined %}
        {% set newparameters = newparameters ~ " TARGET="~params.S %}
      {% endif %}
      SET_TOOL_TEMPERATURE{newparameters}
    {% endif %}
    
  {% else %}
    M104.1 {rawparams}
  {% endif %}
```

### 9. Test print

I created some cubes in Orca, positioned them next to each other, changed their height to 1mm and set each one to a different tool. That allowed me to see if the calculated Z-offset of T1 is good (based off the gcode z offset) and to see if the X and Y are aligned (to test the gcode x and y offsets). It also is a good test for tool changes. This one is with 3 tools:



After doing a longer print with 108 tool changes it's probably good to inspect what else needs adjusting and what broke. I needed to adjust the cup as mentioned to prevent ooze and my wiper on one toolhead broke. The PUG on one toolhead also broke because the umbilical keeps getting snagged under the frame until it violently rebounds. During the print the prime tower also lifted from the bed so more brim was required.



### 10. LED Config for multiple toolheads

Initially I was going to go for [klipper-led-effect](https://github.com/julianschill/klipper-led_effect) and set that up with a working configuration, but unfortunately I got way too many Timer Too Close (TTC) errors during homing/QGL. The CB1 is just not fast enough to process the extra CAN messages in time. I defined the effects per toolhead with a _tN suffix, where N is the tool number and then in all the STATUS_xxxx macros added the suffix based on the current tool (or given T=xx).

I did the same with the static stealthburner_leds.cfg:

```
# Macros for setting the status leds on the Voron StealthBurner toolhead (or for any neopixel-type leds).
#
# You will need to configure a neopixel (or other addressable led, such as dotstar). See
# https://www.klipper3d.org/Config_Reference.html#neopixel for configuration details.

#####################################
#           INSTRUCTIONS            #
#####################################
# How to use all this stuff:
#
#     1.  Copy this .cfg file into your Klipper config directory and then add [include stealthburner_leds.cfg]
#         to the top of your printer.cfg in order to register the LEDs and macros with Klipper.
#     2.  Define your LEDs by editing [neopixel sb_leds] below and entering the data pin from your control board
#         as well as the color order.
#
#           Note: RGB and RGBW are different and must be defined explicitly.  RGB and RGBW are also not able to 
#                 be mix-and-matched in the same chain. A separate data line would be needed for proper functioning.
#
#                 RGBW LEDs will have a visible yellow-ish phosphor section to the chip.  If your LEDs do not have
#                 this yellow portion, you have RGB LEDs.
#
#     3.  Save your config and restart Klipper.
#
#           Note: We set RED and BLUE to 1.0 to make it easier for users and supporters to detect 
#                 misconfigurations or miswiring. The default color format is for Neopixels with a dedicated 
#                 white LED. On startup, all three SB LEDs should light up.
#
#                 If you get random colors across your LEDs, change the color_order to GRB and restart. Then
#                 omit the W for each suggested color_order in the next paragraph.
#
#                 If you get MAGENTA, your  color order is correct. If you get CYAN, you need to use RGBW. If
#                 you get YELLOW, you need to use BRGW (note that BRG is only supported in the latest Klipper
#                 version).
#
#     4.  Once you have confirmed that the LEDs are set up correctly, you must now decide where you want 
#         these macros called up...which means adding them to your existing gcode macros.  NOTHING will happen
#         unless you add the STATUS_????? macros to your existing gcode macros.  
#
#           Example: add STATUS_LEVELING to the beginning of your QGL gcode macro, and then add STATUS_READY 
#                    to the end of it to set the logo LED and nozzle LEDs back to the `ready` state.
#
#           Example: add STATUS_CLEANING to the beginning of your nozzle-cleaning macro, and then STATUS_READY
#                    to the end of it to return the LEDs back to `ready` state.
#
#     5.  Feel free to change colors of each macro, create new ones if you have a need to.  The macros provided below
#         are just an example of what is possible.  If you want to try some more complex animations, you will most
#         likely have to use WLED with Moonraker and a small micro-controller 
#
#####################################
#       END INSTRUCTRUCTIONS        #
#####################################

##########
# MACROS #
##########

# The following status macros are available (these go inside of your macros):
#
#    STATUS_READY
#    STATUS_OFF
#    STATUS_BUSY
#    STATUS_HEATING
#    STATUS_LEVELING
#    STATUS_HOMING
#    STATUS_CLEANING
#    STATUS_MESHING
#    STATUS_CALIBRATING_Z
#
# With additional macros for basic control:
#
#    SET_NOZZLE_LEDS_ON
#    SET_LOGO_LEDS_OFF
#    SET_NOZZLE_LEDS_OFF
#
# Contributed by Voron discord users wile.e, Tetsunosuke, and etherwalker

[gcode_macro _sb_vars]
# User settings for the StealthBurner status leds. You can change the status colors and led
# configurations for the logo and nozzle here.
variable_colors: {
        'logo': { # Colors for logo states
            'busy': {'r': 0.4, 'g': 0.0, 'b': 0.0, 'w': 0.0},
            'cleaning': {'r': 0.0, 'g': 0.02, 'b': 0.5, 'w': 0.0},
            'calibrating_z': {'r': 0.8, 'g': 0., 'b': 0.35, 'w': 0.0},
            'heating': {'r': 0.3, 'g': 0.18, 'b': 0.0, 'w': 0.0},
            'homing': {'r': 0.0, 'g': 0.6, 'b': 0.2, 'w': 0.0},
            'leveling': {'r': 0.5, 'g': 0.1, 'b': 0.4, 'w': 0.0},
            'meshing': {'r': 0.2, 'g': 1.0, 'b': 0.0, 'w': 0.0},
            'off': {'r': 0.0, 'g': 0.0, 'b': 0.0, 'w': 0.0},
            'printing': {'r': 1.0, 'g': 0.0, 'b': 0.0, 'w': 0.0},
            'standby': {'r': 0.01, 'g': 0.01, 'b': 0.01, 'w': 0.1},
            'docking': {'r': 1.0, 'g': 1.0, 'b': 0.0, 'w': 0.0},
        },
        'nozzle': { # Colors for nozzle states
            'heating': {'r': 0.8, 'g': 0.35, 'b': 0.0, 'w':0.0},
            'off': {'r': 0.0, 'g': 0.0, 'b': 0.0, 'w': 0.0},
            'on': {'r': 0.8, 'g': 0.8, 'b': 0.8, 'w':1.0},
            'standby': {'r': 0.6, 'g': 0.0, 'b': 0.0, 'w':0.0},
        },
        'thermal': {
            'hot': {'r': 1.0, 'g': 0.0, 'b': 0.0, 'w': 0.0},
            'cold': {'r': 0.3, 'g': 0.0, 'b': 0.3, 'w': 0.0}
        }
    }
variable_logo_led_name:         "sb_leds" 
# The name of the addressable LED chain that contains the logo LED(s)
variable_logo_idx:              "1" 
# A comma-separated list of indexes LEDs in the logo
variable_nozzle_led_name:       "sb_leds"
# The name of the addressable LED chain that contains the nozzle LED(s). This will
# typically be the same LED chain as the logo.
variable_nozzle_idx:            "2,3"
# A comma-separated list of indexes of LEDs in the nozzle
gcode:
    # This section is required.  Do Not Delete.

[gcode_macro _set_sb_leds]
gcode:
    {% set red = params.RED|default(0)|float %}
    {% set green = params.GREEN|default(0)|float %}
    {% set blue = params.BLUE|default(0)|float %}
    {% set white = params.WHITE|default(0)|float %}
    {% set led = params.LED|string %}
    {% set idx = (params.IDX|string).split(',') %}
    {% set transmit_last = params.TRANSMIT|default(1) %}

    {% for led_index in idx %}
        {% set transmit=transmit_last if loop.last else 0 %}
        set_led led={led} red={red} green={green} blue={blue} white={white} index={led_index} transmit={transmit}
        #RESPOND TYPE='echo' MSG="Setting led {led}, index {led_index} with {red},{green},{blue},{white}, transmit={transmit}"
    {% endfor %}

[gcode_macro _set_sb_leds_by_name]
gcode:
    {% set tool_nr = params.T|default(printer.tool_probe_endstop.active_tool_number)|int %}
    {% set leds_name = params.LEDS %}
    {% set color_name = params.COLOR %}
    {% set color = printer["gcode_macro _sb_vars"].colors[leds_name][color_name] %}
    {% set led = printer["gcode_macro _sb_vars"][leds_name + "_led_name"] ~ "_t" ~ tool_nr|string %}
    {% set idx = printer["gcode_macro _sb_vars"][leds_name + "_idx"] %}
    {% set transmit = params.TRANSMIT|default(1) %}

    _set_sb_leds led={led} red={color.r} green={color.g} blue={color.b} white={color.w} idx="{idx}" transmit={transmit}

[gcode_macro _set_logo_leds]
gcode:
    {% set tool_nr = params.T|default(printer.tool_probe_endstop.active_tool_number)|int %}
    {% set red = params.RED|default(0)|float %}
    {% set green = params.GREEN|default(0)|float %}
    {% set blue = params.BLUE|default(0)|float %}
    {% set white = params.WHITE|default(0)|float %}
    {% set led = printer["gcode_macro _sb_vars"].logo_led_name  ~ "_t" ~ tool_nr|string %}
    {% set idx = printer["gcode_macro _sb_vars"].logo_idx %}
    {% set transmit=params.TRANSMIT|default(1) %}

    _set_sb_leds led={led} red={red} green={green} blue={blue} white={white} idx="{idx}" transmit={transmit}

[gcode_macro _set_nozzle_leds]
gcode:
    {% set tool_nr = params.T|default(printer.tool_probe_endstop.active_tool_number)|int %}
    {% set red = params.RED|default(0)|float %}
    {% set green = params.GREEN|default(0)|float %}
    {% set blue = params.BLUE|default(0)|float %}
    {% set white = params.WHITE|default(0)|float %}
    {% set led = printer["gcode_macro _sb_vars"].nozzle_led_name ~ "_t" ~ tool_nr|string %}
    {% set idx = printer["gcode_macro _sb_vars"].nozzle_idx %}
    {% set transmit=params.TRANSMIT|default(1) %}

    _set_sb_leds led={led} red={red} green={green} blue={blue} white={white} idx="{idx}" transmit={transmit}

[gcode_macro set_logo_leds_off]
gcode:
    {% set tool_nr = params.T|default(printer.tool_probe_endstop.active_tool_number)|int %}
    {% set transmit=params.TRANSMIT|default(1) %}
    _set_logo_leds red=0 blue=0 green=0 white=0 transmit={transmit} T={tool_nr}

[gcode_macro set_nozzle_leds_on]
gcode:
    {% set tool_nr = params.T|default(printer.tool_probe_endstop.active_tool_number)|int %}
    {% set transmit=params.TRANSMIT|default(1) %}
    _set_sb_leds_by_name leds="nozzle" color="on" transmit={transmit} T={tool_nr}

[gcode_macro set_nozzle_leds_off]
gcode:
    {% set tool_nr = params.T|default(printer.tool_probe_endstop.active_tool_number)|int %}
    {% set transmit=params.TRANSMIT|default(1) %}
    _set_sb_leds_by_name leds="nozzle" color="off" transmit={transmit} T={tool_nr}

[gcode_macro status_off]
gcode:
    {% set tool_nr = params.T|default(printer.tool_probe_endstop.active_tool_number)|int %}
    set_logo_leds_off transmit=0 T={tool_nr}
    set_nozzle_leds_off T={tool_nr}

[gcode_macro status_ready]
gcode:
    {% set tool_nr = params.T|default(printer.tool_probe_endstop.active_tool_number)|int %}
    _set_sb_leds_by_name leds="logo" color="standby" transmit=0 T={tool_nr}
    _set_sb_leds_by_name leds="nozzle" color="standby" transmit=1 T={tool_nr}

[gcode_macro status_busy]
gcode:
    {% set tool_nr = params.T|default(printer.tool_probe_endstop.active_tool_number)|int %}
    _set_sb_leds_by_name leds="logo" color="busy" transmit=0 T={tool_nr}
    set_nozzle_leds_on T={tool_nr}

[gcode_macro status_heating]
gcode:
    {% set tool_nr = params.T|default(printer.tool_probe_endstop.active_tool_number)|int %}
    _set_sb_leds_by_name leds="logo" color="heating" transmit=0 T={tool_nr}
    _set_sb_leds_by_name leds="nozzle" color="heating" transmit=1 T={tool_nr}

[gcode_macro status_leveling]
gcode:
    {% set tool_nr = params.T|default(printer.tool_probe_endstop.active_tool_number)|int %}
    _set_sb_leds_by_name leds="logo" color="leveling" transmit=0 T={tool_nr}
    set_nozzle_leds_on T={tool_nr}

[gcode_macro status_homing]
gcode:
    {% set tool_nr = params.T|default(printer.tool_probe_endstop.active_tool_number)|int %}
    _set_sb_leds_by_name leds="logo" color="homing" transmit=0 T={tool_nr}
    set_nozzle_leds_on T={tool_nr}

[gcode_macro status_cleaning]
gcode:
    {% set tool_nr = params.T|default(printer.tool_probe_endstop.active_tool_number)|int %}
    _set_sb_leds_by_name leds="logo" color="cleaning" transmit=0 T={tool_nr}
    set_nozzle_leds_on T={tool_nr}

[gcode_macro status_meshing]
gcode:
    {% set tool_nr = params.T|default(printer.tool_probe_endstop.active_tool_number)|int %}
    _set_sb_leds_by_name leds="logo" color="meshing" transmit=0 T={tool_nr}
    set_nozzle_leds_on

[gcode_macro status_calibrating_z]
gcode:
    {% set tool_nr = params.T|default(printer.tool_probe_endstop.active_tool_number)|int %}
    _set_sb_leds_by_name leds="logo" color="calibrating_z" transmit=0 T={tool_nr}
    set_nozzle_leds_on T={tool_nr}

[gcode_macro status_printing]
gcode:
    {% set tool_nr = params.T|default(printer.tool_probe_endstop.active_tool_number)|int %}
    _set_sb_leds_by_name leds="logo" color="printing" transmit=0 T={tool_nr}
    set_nozzle_leds_on T={tool_nr}

[gcode_macro status_docking]
gcode:
    {% set tool_nr = params.T|default(printer.tool_probe_endstop.active_tool_number)|int %}
    _set_sb_leds_by_name leds="logo" color="docking" transmit=0 T={tool_nr}
    set_nozzle_leds_on T={tool_nr}    
```

I've also added STATUS_DOCKING, which is called in the dropoff and pickup gcode in toolchanger.cfg:
```
STATUS_DOCKING T={tool.tool_number|string}
   .... the rest of the macro ...
M400
STATUS_READY T={tool.tool_number|string}
```

Now at least the leds are set on the correct toolhead

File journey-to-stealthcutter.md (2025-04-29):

# Journey to StealthCutter

## What

The CoreXY motion system of a 3D printer can be used for other things, such as a Vinyl Cutter or plotter. 

## Why

A dedicated Vinyl cutter machine costs a lot, adding a toolhead is maybe 20€. I wanted to try out a cutting head, StealthChanger makes it really easy to swap toolheads, and see if I could cut vinyl, to use as stickers (no surface left untouched with this new power!)

## Details

### Stuff needed
* CB09 blade holder with blades (https://www.aliexpress.com/item/1005007470135620.html)
* Some M3 hardware to mount the backplate and clamp
* Everything you need to put the backplate onto the shuttle (magnet, 2 FHSC's, 3 dowel pins)
* Cutting mat, there are various ones with different glue strength. StandardGrip worked fine for me (https://www.aliexpress.com/item/1005006356387230.html)
* Vinyl sheets, the non thermal variant (I bought https://www.aliexpress.com/item/1005007381981091.html, backing is a bit shit tho)
* Transfer paper (I bought https://www.aliexpress.com/item/1005007081186498.html)

### Toolhead 
[Someone](https://github.com/Telekatz/Voron-Mods/tree/main/Drag%20Knife%20Toolhead) already made a toolhead for a a drag knife, compatible with a TAP plate. As StealthChanger backplates use the same mounting holes I took that as a basis and modified it to be more secure on a StealthBurner backplate

 (with an incorrectly installed blade, see [this video](https://www.youtube.com/watch?app=desktop&v=6PlIlYayNu8) how to install the blade properly, it should stick out only a mm or 2 from the holder.)

### Cutting mat


The cutting mat comes with a sticky surface for the vinyl sheets to adhere to so it doesn't move, there are variations but StandardGrip seems to work fine with vinyl sheets. Unfortunately there is no easy way to secure the cutting mat onto the bed in a way that it doesn't shift. I've tried using N52 magnets and that holds it down relatively well but I still need to give it some extra clamping force with my fingers while it's cutting. Either stronger magnets or some quick release clamps would maybe help.

The toolhead does not have an Octotap and MCU so it can not be automatically docked and picked up. Homing and QGL on the cutting mat which is 0.4mm thick does not become an issue with docking (as the extra offset would put the docks higher than they really are), so it's technically possible to auto dock T0 and pick up the cutter. However some extra macros will be necessary, like a `CUT_START MODE=cut` to set the printer up for cutting, similar to the `PRINT_START`

### Software

With the hardware in place, it was time to find software. [Polycut](https://github.com/IridiumIO/PolyCut) works well to generate Klipper compatible G-code from SVG files and has some nice features. Right now it emits a G28 homing g-code which really should not be done with a sharp blade, the author modified their klipper configuration to home manually, but I can just home and quad gantry level with T0, then dock T0 and put the cutter on.
Removing the G28 is a mandatory extra step.

### Process

There are a fair bit of steps involved:

1)  Home/QGL/Home with T0
2) Dock T0 manually
3) Put on the cutter toolhead
4) Put the cutter mat on the PEI plate if it's not already. Secure with magnets/clamps so it can't shift around (or hold it by hand when it's cutting)
5) Stick the vinyl sheet lightly onto the cutting mat. If the backing of the vinyl is shit it will tear if you press it on too hard
6) Figure out at what Z the cutting is biting into the vinyl. Too high and it won't cut the vinyl all the way through, too low and it will also cut through the backing which holds the parts of vinyl you want in the correct place. Set that Z into Polycut as cutting height.
7) Generate the Gcode. Overcut might be necessary to not have some corners be not entirely cut. Remove the G28 command from the file. 
8) Upload the file and run it, it should cut immediately (I've asked for a preview / trace bounding box feature)
9) Remove cutting mat
10) Remove vinyl sheet from the cutting mat
11) Cut out the part and pry off the vinyl you don't want caaarefully, if it sticks to the vinyl you do want it's basically fucked.
12) Use transfer paper to transfer the vinyl onto the transfer paper.
13) Peel off the backing of the vinyl and stick it onto the surface you want. Make sure to clean the surface so there's no dust/oily fingerprints. 
14) Squeegy it to make sure it adheres properly and remove transfer paper aaand DONE!

## Result

After some trial and error finding the right Z value (too high and it won't cut all the way through the vinyl, too low and it will also cut through the backing holding the vinyl together, I managed to get a decent cut done





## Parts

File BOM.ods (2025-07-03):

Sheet: Overview
Drakarah 3D Printer
Manuals (also see https://github.com/Zev-se/Formbot-voron-2.4-build-guide)
Voron 2.4R2
Voron Stealthburner
Voron TAP
SB2209 CAN
M8P v2.0
BFI/BZI
EBB36
Printed parts are in eSun ABS+ Black and Pink, for the most part and some in eSUN ABS+HS Black
BOM | Qty | Description | Type | Total | Comments
Frame
Frame | 8 | A Extrusion (470mm) | Extrusion | 8
 | 4 | B Extrusion (530mm) | Extrusion | 4
 | 16 | M5x16 BHCS | Fastener | 16
 | 1 | Aluminium slot cover tubing black | Sealant | 1
Bed support | 2 | A Extrusion (470mm) | Extrusion | 2
 | 4 | M5 x16 BHCS | Fastener | 4
 | 4 | OpenBuilds Billet Angle Corner Connector (2020) | Fastener | 4
 | 4 | M5 T-Nut | Fastener | 4
 | 4 | M5x10 BHCS | Fastener | 4
 | 4 | M5 Shim | Fastener | 4
Z drives
Linear rails | 4 | Linear rail MGN9H (400mm) | Rail | 4
 | 32 | M3 T-Nut | Fastener | 32
 | 32 | M3x8 BHCS | Fastener | 32
Deck panel | 4 | M5 T-Nut | Fastener | 4
 | 1 | Deck panel (469x469x4mm) | Panel | 1
 | 2 | DIN rails |  | 2
 | 4 | M5x10 BHCS | Fastener | 4
Drive | 36 | Heat Insert |  | 36 | Make sure set screws are against the flat part of the shaft with thread locker
(4 in total) | 2 | z_drive_main_a_x2.stl | 3D print | 2 | And belt tension is such with the motor that there is no backlash
 | 2 | z_drive_retainer_a_x2.stl | 3D print | 2
 | 2 | z_drive_main_b_x2.stl | 3D print | 2
 | 2 | z_drive_retainer_b_x2.stl | 3D print | 2
 | 4 | 5x60 shaft (D cut) |  | 4
 | 4 | GT2 20T 9mm wide pulley | Pulley | 4
 | 12 | 625 Bearing | Bearing | 12
 | 16 | M5 Shim | Fastener | 16
 | 4 | GT2 80 Tooth pulley | Pulley | 4
 | 4 | GT2 belt loop 6mm wide 188mm | Belt | 4
 | 24 | M3x40 SHCS | Fastener | 24
 | 2 | [a]_z_drive_baseplate_a_x2.stl | 3D print | 2
 | 2 | [a]_z_drive_baseplate_b_x2.stl | 3D print | 2
 | 4 | M5 Nut | Fastener | 4
 | 12 | M3x8 BHCS | Fastener | 12
 | 8 | M5 T-Nut | Fastener | 8
 | 8 | M5x40 SHCS | Fastener | 8
 | 4 | Rubber foot |  | 4
 | 4 | M5x16 BHCS | Fastener | 4
Motor | 4 | Nema17 Stepper motor (moons-ms17hd6p420I-04) | Motor | 4
 | 4 | GT2 16 Tooth pulley | Pulley | 4
 | 2 | z_motor_mount_a_x2.stl | 3D print | 2
 | 2 | z_motor_mount_b_x2.stl | 3D print | 2
 | 2 | [a]_belt_tensioner_a_x2.stl | 3D print | 2
 | 2 | [a]_belt_tensioner_b_x2.stl | 3D print | 2
 | 12 | M3x8 SHCS | Fastener | 12
 | 8 | M5 T-Nut | Fastener | 8
 | 8 | M5x10 BHCS | Fastener | 8
Z idler
BZI | 4 | BZI_V2.4_idler_body_x4.stl | 3D print | 4 | (https://github.com/clee/VoronBFI)
 | 4 | [a]_BZI_V2.4_carrier_x4.stl | 3D print | 4
 | 8 | M5 Nut | Fastener | 8
 | 8 | M5x30 BHCS | Fastener | 8
 | 4 | GT2 20T 9mm idler pulley | Pulley | 4
 | 4 | 5x22mm pin | Fastener | 4
 | 8 | M5X40 SHCS with shim | Fastener | 8 | (these should be M5x40 BHCS but I didn't have any)
 | 8 | M5 T-Nut | Fastener | 8
Bed
 | 1 | Aluminium bed 350x350 | Bed | 1
 | 1 | Bed heater | Bed | 1
 | 1 | Magnetic sheet | Bed | 1
 | 1 | M3 washer | Fastener | 1
 | 1 | M3x12 SHCS | Fastener | 1
 | 1 | M3x6 BHCS | Fastener | 1
 | 4 | M3 T-Nut | Fastener | 4
 | 4 | Bakelite spacers | Bed | 4
 | 4 | M3x12 SHCS | Fastener | 4 | (used smaller ones instead of 16mm so they are not sticking out)
 | 1 | Textured/smooth PEI plate | Bed | 1
Bed/PEI guide pins | 2 | M5x30 pin external thread | Fastener | 2 | Any M5 screw would do too but I had these for the sexball
 | 2 | M5 T-Nut | Fastener | 2
Gantry
Drives | 1 | a_drive_frame_lower.stl | 3D print | 1
(2 in total) | 1 | a_drive_frame_upper.stl | 3D print | 1
 | 1 | b_drive_frame_upper.stl | 3D print | 1
 | 1 | b_drive_frame_lower.stl | 3D print | 1
 | 4 | Heat Insert | Fastener | 4
 | 4 | M5x30 BHCS | Fastener | 4
 | 12 | F695 Bearing | Bearing | 12
 | 12 | M5 Shim | Fastener | 12
 | 2 | Nema17 Stepper motor (moons-ms17hd6p420I-04) | Motor | 2
 | 2 | GT2 20 Tooth Pulley | Pulley | 2
 | 6 | M3x30 SHCS | Fastener | 6
Mini BFI | 2 | Heat Insert | Fastener | 2 | (https://github.com/DraftShift/StealthChanger/tree/main/UserMods/BT123/MiniBFI%20%2B%20MicroBFI)
 | 4 | MiniBFI Belt_Clamp x4.stl | 3D print | 4
 | 2 | MiniBFI Carrier x2.stl | 3D print | 2
 | 2 | MiniBFI Front_Cover x2.stl | 3D print | 2
 | 2 | MiniBFI Housing x2.stl | 3D print | 2
 | 4 | M3x16 BHCS | Fastener | 4
 | 2 | M5x16 BHCS | Fastener | 2
 | 2 | M5 T-Nut | Fastener | 2
 | 2 | M3 T-Nut | Fastener | 2
 | 4 | F695 bearing | Bearing | 4
 | 4 | M5 Shim | Fastener | 4
 | 2 | 5x18mm pin | Fastener | 2
Gantry | 1 | E extrusion (430mm) | Extrusion | 1
 | 8 | M5 T-Nut | Fastener | 8
 | 8 | M5x10 BHCS | Fastener | 8
 | 2 | Linear rail MGN9H (400mm) | Rail | 2
 | 16 | M3 T-Nut | Fastener | 16
 | 16 | M3x8 SHCS | Fastener | 16
 | 2 | C extrusion (450mm) | Extrusion | 2
 | 8 | M5 T-Nut | Fastener | 8
 | 4 | M3 T-Nut | Fastener | 4
 | 4 | M5 T-Nut | Fastener | 4
 | 4 | [a]_z_belt_clip_upper_x4.stl | 3D print | 4
 | 8 | M5x16 BHCS | Fastener | 8
XY Joints | 1 | xy_joint_left_lower_MGN12.stl | 3D print | 1
 | 1 | xy_joint_left_upper_MGN12.stl | 3D print | 1
 | 1 | xy_joint_right_lower_MGN12.stl | 3D print | 1
 | 1 | xy_joint_right_upper_MGN12.stl | 3D print | 1
 | 6 | M5 Nut | Fastener | 6
 | 4 | F695 Bearing | Bearing | 4
 | 4 | M5 Shim | Fastener | 4
 | 2 | M5x40 SHCS | Fastener | 2
 | 6 | M5x40 SHCS | Fastener | 6
 | 2 | GT20 Tooth Idler | Pulley | 2
X axis | 1 | D extrusion (340mm) | Extrusion | 1
 | 1 | Linear rail MGN12H (400mm) | Rail | 1
 | 6 | M3 T-Nut | Fastener | 6
 | 6 | M3x8 SHCS | Fastener | 6
 | 6 | M5 T-Nut | Fastener | 6
 | 4 | M5x10 BHCS | Fastener | 4 | (no cable guide)
 | 2 | M5x30 BHCS | Fastener | 2
 | 2 | M5 Shim | Fastener | 2
 | 8 | M3x16 SHCS | Fastener | 8
Gantry mount | 4 | z_joint_upper_x4.stl | 3D print | 4
 | 4 | M5 Nut | Fastener | 4
 | 4 | GT2 Belt 9mm wide (1200mm) | Belt | 4
 | 4 | [a]_z_belt_clip_lower_x4.stl | 3D print | 4
 | 4 | M3x30 SHCS | Fastener | 4
 | 4 | M5x30 BHCS | Fastener | 4
 | 4 | z_joint_lower_x4.stl | 3D print | 4
 | 16 | M3x20 SHCS | Fastener | 16
 | 4 | M5x40 SHCS | Fastener | 4
A/B belts | 2 | GT2 Belt 6mm wide (2000mm) | Belt | 2
Toolhead |  |  |  |  | (https://github.com/VoronDesign/Voron-Stealthburner/)
Stealthchanger shuttle | 1 | Shuttle MGN12 (Without belt grooves).stl | 3D print | 1 | (https://github.com/DraftShift/StealthChanger)
 | 1 | Shuttle_Keeper_9mm_MGN12H.stl | 3D print | 1
 | 3 | Bushings 4ID x 6OD x 6mm | Fastener | 3
 | 3 | 6x3mm N52 magnet | Magnet | 3
 | 1 | Heat Insert | Fastener | 1
 | 2 | M3x40 SHCS | Fastener | 2
 | 4 | M3x12 BHCS | Fastener | 4 | For attaching to carriage through shuttle keeper, must be BHCS
Stealtchanger backplate | 1 | StealthBurner.stl | 3D print | 4 | An extra backplate for the vinyl cutter toolhead, this does not use octotap atm
 | 4 | Heat Insert | Fastener | 16
 | 3 | Dowel pin 4OD x 12mm | Fastener | 12
 | 1 | 6x3mm N52 magnet | Magnet | 4
 | 2 | M3x8 FHCS (magnetic) | Fastener | 8
 | 1 | Octotap PCB | PCB | 3
 | 2 | M3x6 BHCS | Fastener | 6
Belt helper | 1 | Left Block.stl | 3D print | 1
 | 1 | Left Clip.stl | 3D print | 1
 | 1 | Right Block.stl | 3D print | 1
 | 1 | Right Clip.stl | 3D print | 1
 | 6 | Heat Insert | Fastener | 6
 | 4 | M3x10 SHCS | Fastener | 4
 | 2 | M3x20 SHCS | Fastener | 2
Clockwork 2 | 12 | Heat Insert | Fastener | 36
 | 1 | [a]_guidler_a.stl | 3D print | 3
 | 1 | [a]_guidler_b.stl | 3D print | 3
 | 1 | M3x16 SHCS | Fastener | 3
 | 1 | BMG gears (idler, thumbscrew, 2MR85 bearing) |  | 3
 | 1 | [a]_latch_shuttle.stl | 3D print | 3
 | 1 | motor_plate.stl | 3D print | 3
 | 1 | main_body.stl | 3D print | 3
 | 1 | M3x6 FHCS | Fastener | 3
 | 2 | M3x25 SHCS | Fastener | 6
 | 1 | M3x25 SHCS | Fastener | 3
 | 1 | [a]_latch.stl | 3D print | 3
 | 1 | M3x25 SHCS | Fastener | 3
 | 1 | Nema 14 pancake stepper (CSE14HRA1L410A) | Motor | 3
 | 1 | M3x30 SHCS | Fastener | 3
 | 1 | M3x8 SHCS | Fastener | 3
 | 1 | M3 Washer | Fastener | 3
 | 3 | Heat Insert | Fastener | 9
 | 1 | sb2240_holder_partA_remixed.stl | 3D print | 3 | (https://www.printables.com/model/825825-sb2209-sb2240-mount-for-pug-new-plug)
 | 1 | sb2240_holder_partB.stl.stl | 3D print | 3
 | 1 | M3x20 SHCS | Fastener | 3
 | 1 | M3x8 SHCS | Fastener | 3
 | 2 | PUG_v4_M_7.0mm.stl | 3D print | 6 | (https://www.printables.com/model/378567-pug-parametric-umbilical-gland)
 | 2 | M3x12 SHCS | Fastener | 6
 | 1 | M3x16 SHCS | Fastener | 3
 | 1 | cable_door_for_pcb.stl | 3D print | 3
 | 1 | M3x6 BHCS | Fastener | 3
 | 1 | [a]_pcb_spacer.stl | 3D print | 2
 | 1 | SB2209 PCB | PCB | 2
 | 2 | M3x10 BHCS | Fastener | 4
 | 1 | EBB36 PCB | PCB | 1
 | 1 | EBB36 mount base.stl | 3D print | 1 | (https://www.printables.com/model/1126741-ebb36-v12-cw2-mount-with-pug)
 | 1 | EBB36 mount retainer.stl | 3D print | 1
 | 1 | M3x40 SHCS | Fastener | 1
 | 1 | M3x16 SHCS | Fastener | 1
Tool cartridge | 1 | stealthburner_printhead_dragon_front.stl | 3D print | 1
 | 1 | stealthburner_printhead_dragon_rear_cw2.stl | 3D print | 1
 | 1 | stealthburner_printhead_v6_r6_front.stl | 3D print | 2
 | 1 | stealthburner_printhead_v6_r6_rear_cw2.stl | 3D print | 2
 | 2 | Heat Insert | Fastener | 6
 | 2 | M3x16 SHCS | Fastener | 6
 | 1 | Dragon HF hotend | Hotend | 1
 | 2 | V6 Clone hotend | Hotend | 2
 | 1 | 2mm OD PTFE Tube | Filament routing | 3
Stealthburner | 1 | [a]_stealthburner_main_body.stl | 3D print | 3
 | 1 | [o]_stealthburner_LED_carrier.stl | 3D print | 3
 | 1 | [c]_stealthburner_LED_diffuser.stl | 3D print | 3 | (I don't have a resin print so I used a bit of panel diffuse protective plastic, that works fine too)
 | 1 | Neopixel LED wiring |  | 3
 | 1 | 4010 Fan | Fan | 3
 | 1 | 5015 Blower Fan | Fan | 3
 | 1 | SB0000 PCB | PCB | 2
 | 2 | M3x6 FHCS | Fastener | 6
Electronics
Core | 1 | M8P v2.0 PCB | PCB | 1
 | 1 | CB1 module | PCB | 1
 | 1 | Manta_M8P_2pc.stl | 3D print | 1 | (https://github.com/FORMBOT/Voron-2.4/tree/main/STL/Primary)
 | 4 | M2.5x6 BHCS | Fastener | 4 | (comes with m8p)
 | 1 | PSU LRS-250-24 | PCB | 1
 | 1 | lrs_200_psu_bracket_x2.stl | 3D print | 1
 | 4 | M4x6 BHCS | Fastener | 4
 | 1 | PSU_stabilizer_50mm.stl | 3D print | 1
 | 1 | M5 T-Nut | Fastener | 1
 | 1 | M4x6 BHCS | Fastener | 1
 | 1 | M5x10 BHCS | Fastener | 1
 | 1 | 3-6.stl | 3D print | 1
 | 1 | power_inlet_filtered.stl | 3D print | 1
 | 5 | Heat Insert | Fastener | 5
 | 1 | AC switch |  | 1
 | 1 | Filtered inlet |  | 1
 | 1 | Medium Blow Fuse 5x20mm 4A |  | 1
 | 1 | C13 Power Cord | Wiring | 1
 | 2 | M3x10 FHCS | Fastener | 2
 | 2 | M3 T-Nut | Fastener | 2
 | 2 | M3x8 SHCS | Fastener | 2
 | 1 | Omron SSR with relay mount | PCB | 1
 | 2 | M4x6 BHCS | Fastener | 2
Peripherals interfaces | 2 | USB cable male to male | Wiring | 2
 | 1 | Ethernet cable male to male | Wiring | 1
 | 2 | USB Keystone |  | 2
 | 1 | Ethernet Keystone |  | 1
 | 1 | Voron Skirt Keystone-Inside.stl | 3D print | 1 | (https://www.printables.com/model/609433-voron-skirt-keystone-for-usbethernet/files)
 | 1 | Voron Skirt Keystone-Outside.stl | 3D print | 1 | I had to modify them to make them fit
 | 1 | USB splitter 4 way | Wiring | 1
 | 1 | USB webcam |  | 1
Wago CAN distribution | 1 | WAGO_5_DIN V2.stl | 3D print | 1 | (https://www.printables.com/model/619371-wago-221-din-mount-2-3-5/files)
 | 4 | Wago 221 2 way | Wiring | 4 | (to connect the back umbilical to 24v and CAN)
 | 4 | Wago 221 5 way | Wiring | 4
 | 1 | CAN exhaust box.step (base) | 3D print | 1 | (https://www.printables.com/model/1119606-wago-can-distribution-box-for-n3mi-umbilical-plate)
 | 1 | CAN exhaust box.step (lid) | 3D print | 1
 | 2 | Wago_221_415_x2.stl | 3D print | 2 | (https://www.printables.com/model/506687-wago-221-415-mount)
 | 6 | Bowden coupler |  | 6 | I've added these after the fact because the PTFE tubes were getting kinked by drilling a hole into the lid and then forcibly threading them in
Umbilical and cable chains
Back umbilical | 1 | CAN Cable | Wiring | 1
 | 2 | 1.5mm² wire | Wiring | 2
 | 1 | Cable sleeve (8mm) | Wiring | 1
 | 2 | PUG_v4_M_8.5mm.stl | 3D print | 2 | (https://www.printables.com/model/378567-pug-parametric-umbilical-gland)
Toolhead umbilical | 1 | PG7_6_tool_350mm.stl | 3D print | 1 | (https://github.com/DraftShift/CableManagement/tree/main/UserMods/N3MI-DG/Umbilical_Plates), I added a hole for the thermistor
 | 2 | M5 T-Nut | Fastener | 2
 | 2 | M5x10 BHCS | Fastener | 2
Per toolhead | 2 | Piano wire | Wiring | 6
 | 1 | Cable sleeve (8mm) | Wiring | 3 | (https://www.aliexpress.com/item/1005007407008905.html)
 | 1 | PTFE Tube ID 3mm OD 4mm (1m) | Filament routing | 3
 | 1 | PG-7 gland | Fastener | 3
 | 1 | CAN cable (80cm) | Wiring | 3
Z cable chain | 1 | TopClamp.stl | 3D print | 1 | https://www.printables.com/model/1140907-brackets-for-z-umbilical-with-pug
 | 1 | TopPUGRetainer.stl | 3D print | 1
 | 1 | BottomClamp.stl | 3D print | 1
 | 1 | BottomPUGRetainer.stl | 3D print | 1
 | 4 | Heat Insert | Fastener | 4
 | 4 | M3x16 SHCS | Fastener | 4
 | 4 | M3 Hammer T-Nut | Fastener | 4
 | 4 | M3x8 SHCS | Fastener | 4
 | 1 | Cable shroud | Wiring | 1
Skirts
Core | 1 | rear_center_skirt_350.stl | 3D print | 1
 | 2 | side_skirt_a_350_x2.stl | 3D print | 2
 | 2 | side_skirt_b_350_x2.stl | 3D print | 2
 | 1 | front_skirt_a_350.stl | 3D print | 1
 | 1 | front_skirt_b_350.stl | 3D print | 1
 | 1 | keystone_panel.stl | 3D print | 1
 | 2 | side_fan_support_x2.STL | 3D print | 2
 | 2 | [a]_fan_grill_retainer_x2.stl | 3D print | 2
 | 27 | Heat Insert | Fastener | 27
 | 2 | 6020 Fan | Fan | 2
 | 2 | [a]_belt_guard_a_x2.stl | 3D print | 2
 | 2 | [a]_belt_guard_b_x2.stl | 3D print | 2
 | 8 | M3x8 SHCS | Fastener | 8
 | 10 | M3 T-Nut | Fastener | 10 | Should have gone with M3 Hammer nuts for the skirts
 | 10 | M3x8 SHCS | Fastener | 10
 | 16 | M3x8 SHCS | Fastener | 16
 | 4 | M3x8 SHCS | Fastener | 4
 | 4 | M3 T-Nut | Fastener | 4
 | 2 | M5 T-Nut | Fastener | 2
 | 4 | M3x8 SHCS | Fastener | 4
 | 2 | M5x10 BHCS | Fastener | 2
LCD | 1 | BTT 5" HDMI screen |  | 1
 | 1 | btt_hdmi5_hidden_connector.stl | 3D print | 1 | (https://www.printables.com/model/612525-btt-hdmi5-mount-conector-hide)
 | 1 | Voron Mount for Hdmi5 Screen Holder.stl | 3D print | 1 | (https://www.printables.com/model/415066-bigtreetech-hdmi5-screen-mount-for-voron-24/files)
 | 6 | M3x12 SHCS | Fastener | 6
 | 2 | M3 T-Nut | Fastener | 2
Z belt covers
 | 2 | z_belt_cover_a_x2.stl | 3D print | 2
 | 2 | z_belt_cover_b_x2.stl | 3D print | 2
 | 4 | M3x6 BHCS | Fastener | 4
 | 4 | M3 T-Nut | Fastener | 4 | Should have also probably gone with hammerhead Nuts
Panels
Bottom panel | 1 | Polycarbonate panel black (483x503x4) | Panel | 1
 | 6 | bottom_panel_clip_x4.stl | 3D print | 6
 | 6 | M3x12 SHCS | Fastener | 6
Back panel | 1 | Polycarbonate panel black | Panel | 1
 | 1 | 1mm foam tape | Sealant | 1
 | 4 | corner_panel_clip_4mm_x8.stl | 3D print | 4
 | 3 | midspan_panel_clip_4mm_x7.stl | 3D print | 3
 | 11 | M3x8 SHCS | Fastener | 11
 | 11 | M3 Hammer T-Nut | Fastener | 11
Side panels | 2 | Polycarbonate panel clear (483x503x3 mm) | Panel | 2
 | 2 | 3mm foam tape | Sealant | 2
Tough latches | 22 | tough_handle_1_8mm_holes.stl | 3D print | 22 | (https://www.printables.com/model/1061047-tough-latches-with-space-for-18mm-dowel-pins)
 | 88 | 1.5mm x 12mm pin | Fastener | 88
 | 88 | M3x4 set screw | Fastener | 88 | I would forego those set screws and just use superglue, these set screws make it way to easy to crack the plastic
 | 22 | M3x12 SHCS | Fastener | 22
 | 22 | M3 Hammer T-Nut | Fastener | 22
Top panel | 1 | Polycarbonate panel clear (483x483x3 mm) | Panel | 1 | The top panel is installed on the top hat in the same way as it was on the frame
 | 1 | 1mm foam tape | Sealant | 1
 | 4 | corner_panel_clip_4mm_x8.stl | 3D print | 4
 | 8 | M3x8 SHCS | Fastener | 8
 | 8 | M3 Hammer T-Nut | Fastener | 8
The filter |  |  |  |  | (https://www.printables.com/model/334276-the-filter-for-voron-24)
Main cartridge | 1 | Activated carbon (acid free) |  | 1 | Not used the ones that came with Formbot because those are tinier pellets
 | 1 | TheScrewFilter.step | 3D print | 1 | (https://www.printables.com/model/947574-the-screw-filter)
 | 1 | The Filter_Stock_Lid_1_1.stl | 3D print | 1 | (https://www.printables.com/model/334276-the-filter-for-voron-24)
 | 2 | Wago 221 2 way | Wiring | 2
 | 2 | 50x15 blower fan | Fan | 2
 | 2 | M3x25 SHCS | Fastener | 2
 | 2 | M3 T-Nut | Fastener | 2
Side bed fans | 1 | TheFilter-Single_Left_Fixed_Front_Mount.stl | 3D print | 1 | (https://www.printables.com/model/951275-the-filter-front-mounted-side-fans)
 | 1 | TheFilter-Single_Right_Fixed_Front_Mount.stl | 3D print | 1
 | 1 | The_Filter_Single_Left Side Lid.stl | 3D print | 1
 | 1 | The_Filter_Single_Right Side Lid.stl | 3D print | 1
 | 4 | M3x25 SHCS | Fastener | 4
 | 4 | M3 T-Nut | Fastener | 4
 | 2 | 50x15 blower fan | Fan | 2
LED Bar
 | 1 | LED Bar |  | 1
 | 1 | led_holder_b_formbot_with_slit.stl | 3D print | 1 | (https://www.printables.com/model/1083956-formbot-led-bar-holder-with-slit)
 | 1 | led_holder_b_formbot_with_slit.stl (mirror) | 3D print | 1
 | 2 | M3x20 SHCS | Fastener | 2
 | 2 | M3 Hammer T-Nut | Fastener | 2
Nozzle wiper
 | 1 | BambuWiperBetweenTheFilterFans-Container.stl | 3D print | 1 | (https://www.printables.com/model/1133796-bambu-nozzle-brush-with-tray-between-the-filter-be/files)
 | 1 | BambuWiperBetweenTheFilterFans-Wiper holder.stl | 3D print | 1
 | 1 | Bambu lab A1 silicone brush |  | 1
 | 1 | M3x8 SHCS | Fastener | 1
 | 1 | M3 T-Nut | Fastener | 1 | Use hammerhead nuts in case you ever need to move it
Clicky clack door |  |  |  |  | (https://github.com/tanaes/whopping_Voron_mods/tree/main/clickyclacky_door)
 | 2 | A Extrusion (470mm) | Extrusion | 2
 | 2 | B Extrusion (530mm) | Extrusion | 2
 | 1 | Polycarbonate panel (480x500) | Panel | 1
 | 6 | M5x7x8 Split bushing | Fastener | 6
 | 4 | M5x45 Dowel pin | Fastener | 4
 | 4 | M3x20 SHCS | Fastener | 4
 | 12 | M3x8 SHCS | Fastener | 12
 | 12 | 6x3mm magnet | Magnet | 12
 | 1 | Heat Insert | Fastener | 1
 | 4 | M5x16 BHCS | Fastener | 4
 | 1 | Handle-Hinge_Bottom.stl | 3D print | 1
 | 1 | Handle-Hinge_Top.stl | 3D print | 1
 | 1 | Handle.stl | 3D print | 1
 | 2 | Hinge-L-sleeve-2X.stl | 3D print | 2
 | 2 | Hinge-L-solid-2X.stl | 3D print | 2
 | 1 | Latch.stl | 3D print | 1
 | 4 | 2020-Extrusion-end-cap.step | 3D print | 4 | (https://www.printables.com/model/642540-2020-end-cap-with-chamfer)
 | 1 | D weather strip | Sealant | 1
Handles
 | 2 | [a]_handle_middle_part.stl | 3D print | 2 | (https://mods.vorondesign.com/details/xa84lhUN5aMX4nmfZquaQ)
 | 2 | handle_inner_part.stl | 3D print | 2
 | 2 | handle_outer_part.stl | 3D print | 2
 | 2 | Voron-1-R-Handle-Spacer-Body001.stl | 3D print | 2 | (https://www.printables.com/model/1098129-top-hat-spacer-for-voron-handle-by-1-0-r)
 | 10 | M5 T-Nut | Fastener | 10
 | 4 | M5x30 BHCS | Fastener | 4
 | 6 | M5x40 BHCS | Fastener | 6
 | 6 | Heat Insert | Fastener | 6
 | 6 | M3x12 SHCS | Fastener | 6
Top hat
 | 7 | A Extrusion (470mm) | Extrusion | 7 | (could also be 8, but I ordered 8 and used one for the crossbar)
 | 4 | Extrusion (240mm) | Extrusion | 4 | technically you could do without the bottom extrusions so you would only need 4 but it's a lot harder to plunk the top hat onto the frame straight then
 | 16 | Corner brackets | Fastener | 16
 | 16 | M5 Hammerhead T-nut | Fastener | 16
 | 16 | M5x8 BHCS | Fastener | 16
 | 4 | Polycarbonate panel (240x480) | Panel | 4
 | 1 | 1mm foam tape | Sealant | 1 | The side panels don't have enough clearance with the handles to have 3mm foam so 1mm it is
 | 1 | 3mm foam tape | Sealant | 1
 | 4 | TopHatSpacer_v2.step | 3D print | 4
 | 4 | dowelpin.step | 3D print | 4
 | 4 | midspan_panel_clip_4mm_x7.stl | 3D print | 4
 | 4 | corner_panel_clip_4mm_x8.stl | 3D print | 4
 | 4 | corner_panel_clip_6mm_x8.stl | 3D print | 4
 | 4 | midspan_panel_clip_6mm_x8.stl | 3D print | 4
 | 8 | M3x8 SHCS | Fastener | 8
 | 8 | M3x12 SHCS | Fastener | 8
 | 16 | M3 Hammer T-Nut | Fastener | 16
 | 1 | D weather strip | Sealant | 1
 | 1 | U weather strip | Sealant | 1 | (for front panel as that one has no extrusion to rest on)
Modular docks
Crossbar | 1 | A Extrusion (470mm) | Extrusion | 1 | For crossbar
 | 2 | Corner brackets | Fastener | 2 | (https://www.aliexpress.com/item/1005007349855293.html)
 | 4 | M5 Hammerhead T-nut | Fastener | 4
 | 4 | M5x8 BHCS | Fastener | 4
Dock (per dock) | 1 | Bottom.stl | 3D print | 3 | (https://github.com/DraftShift/ModularDock)
 | 1 | Crab left.stl | 3D print | 3 | (https://www.printables.com/model/994635-stealthchanger-stealthburner-minimal-docks-aka-hap)
 | 1 | Crab right.stl | 3D print | 3
 | 2 | Heat Insert | Fastener | 6
 | 4 | M3x16 SHCS | Fastener | 12
 | 4 | Heat Insert | Fastener | 12
 | 2 | M3x50 SHCS | Fastener | 6
 | 2 | M3x20 SHCS | Fastener | 6
 | 1 | Stealthburner Back.stl | 3D print | 3
 | 1 | Stealthburner Base.stl | 3D print | 3
 | 1 | Heat Insert | Fastener | 3
 | 2 | M3x10 SHCS | Fastener | 6
 | 4 | Heat Insert | Fastener | 12
 | 1 | Cup.stl | 3D print | 3
 | 1 | Cup_Body.stl | 3D print | 3
 | 4 | M3x30 SHCS | Fastener | 12
 | 1 | BambuNozzleWiper.stl | 3D print | 3 | Wiper
 | 1 | PTFE Tube ID 2mm OD 4mm | Filament routing | 3
 | 1 | M4 spring (ballpen spring) | Fastener | 3
 | 1 | M3x16 SHCS | Fastener | 3
 | 1 | L_Bracket.stl | 3D print | 3
 | 2 | M5x10 SHCS | Fastener | 6 | BHCS is listed but I didn't have any
 | 2 | M3x8 BHCS | Fastener | 6
 | 2 | M5x10 SHCS | Fastener | 6 | Attaching to crossbar
 | 2 | M5 T-Nut | Fastener | 6
 | 2 | M3x12 SHCS | Fastener | 6 | Locking the tool in place, I tried the 5x2mm magnets but they are not strong enough at all to keep the tools in place
Tool alignment
Z endstop | 1 | HartK probe | PCB | 1
 | 2 | M3x16 SHCS | Fastener | 2
Axiscope | 1 | OV9726 Camera module | PCB | 1 | https://www.printables.com/model/1099576-xy-nozzle-alignment-camera/files
 | 1 | OV9726 Case.stl | 3D print | 1
 | 4 | 5V white leds | PCB | 4
Cutter
Toolhead | 1 | dragknife_stealthchanger_tap.step | 3D print | 1 | (https://www.printables.com/model/1286354-drag-knife-toolhead-compatible-with-stealthchanger)
 | 1 | dragknife_sc_sbbackplate-Drag Knife ToolheadDrag Knife Slider Front.step | 3D print | 1
 | 1 | dragknife_stealthchanger_spacer.step | 3D print | 1
 | 2 | M3x8 SHCS | Fastener | 2
 | 2 | M3x16 SHCS | Fastener | 2
 | 1 | CB09 Drag Knife |  | 1 | (https://www.aliexpress.com/item/1005007470135620.html)
 | 2 | Heat Insert | Fastener | 2
Other | 1 | Transfer paper |  | 1
 | 1 | Standardgrip cutting mat |  | 1
Filament rollers
 | 20 | Spool_roller_sides_narrow.stl | 3D print | 20 | (https://www.printables.com/model/73636-filament-spool-roller-w-608-bearings)
 | 20 | Spool_roller_bottom_narrow.STL.stl | 3D print | 20
 | 20 | Bearing_roller_guides_v1.STL | 3D print | 20
 | 1 | Rail.stl | 3D print | 1
 | 2 | RailClampForFilamentSpoolHolder-Rail clamp.stl | 3D print | 2 | (https://www.printables.com/model/1287401-filament-spool-holder-rail-clamp/files)
 | 2 | M3x12 SHCS | Fastener | 2
 | 2 | M3 Hammer T-Nut | Fastener | 2
 | 20 | 608 bearings |  | 20 | Bought bearings but didn't have enough, so I printed some https://www.printables.com/model/561588-bearings-print-in-place-with-real-rolling-elements
 | 1 | voron-filament-guide.stl | 3D print | 1 | (https://www.printables.com/model/841999-voron-filament-guide-to-fit-spool-arm)

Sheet: Sheet1
Old stuff swapped out
TAP carrier plate | 1 | Linear rail MGN9 50mm
 | 1 | [a]_Tap_Center_r8.stl
 | 4 | 6x3mm magnet | (used 4 magnets instead of 2 M3 FHCS as the magnets were rather weak)
 | 1 | Tap_Center_left_r8.stl
 | 1 | Tap_Center_right_r8.stl
 | 8 | Heat Insert
 | 1 | Tap_Upper_PCB_r8.stl
 | 1 | M3 Nut
 | 2 | M3x20 SHCS
 | 2 | M3x16 SHCS
 | 2 | M3x12 SHCS
 | 2 | M3x6 BHCS
 | 2 | M3x10 BHCS
 | 2 | M3 Washer
 | 1 | Heat Insert
 | 1 | M3x16 SHCS
 | 2 | M3x50 SHCS
 | 1 | M3x6 SHCS
 | 1 | M3x8 SHCS
 | 4 | M3x6 BHCS
 | 4 | M3 Washer
 | 2 | [a]_Tap_Belt_Cover_r8_x2.stl
 | 2 | M3x8 SHCS
 | 2 | M3 Nut
 | 2 | M3 Washer
 | 1 | Optotap V2.4.1 PCB
Mount to TAP plate | 2 | M3x8 SHCS
 | 2 | M3x25 SHCS
 | 2 | M3x50 SHCS
Idlers | 4 | Heat Insert
 | 1 | front_idler_left_lower.stl
 | 1 | front_idler_left_upper.stl
 | 1 | [a]_tensioner_left.stl
 | 1 | front_idler_right_lower.stl
 | 1 | front_idler_right_upper.stl
 | 1 | [a]_tensioner_right.stl
 | 4 | M5 Nut
 | 2 | M5x40 SHCS
 | 4 | M5 Shim
 | 4 | F695 bearing
 | 2 | M3 Washer
 | 2 | M3x40 SHCS
Nevermore |  |  |  |  | (https://github.com/nevermore3d/Nevermore_Micro/blob/master/README.md#bom-v5)
 | 1 | Activated carbon (acid free) |  | 4
 | 1 | Duo_Plenum_wago.stl | 3D print | 4 | (https://github.com/FORMBOT/Voron-2.4/tree/main/STL/Primary/Nevermore)
 | 1 | Duo_Plenum_Lid.stl | 3D print | 24
 | 1 | XL_Cartridge_Lid(contributed_by_Bucknova).3mf | 3D print | 2
 | 1 | Duo_Cartridge_XL.stl | 3D print | 2
 | 2 | 50x15 blower fan | Fan | 4
 | 6 | Heat Insert | Fastener | 12
 | 8 | 6x3mm magnet | Magnet | 8
 | 4 | M3x16 BHCS | Fastener | 8
 | 1 | M3x6 BHCS | Fastener | 4
 | 2 | M3x12 SHCS | Fastener | 4
 | 2 | M3 T-Nut | Fastener | 0
Dock (per dock) | 1 | Left.stl | 3D print | 12
 | 1 | Right.stl | 3D print | 6
 | 1 | Bottom.stl | 3D print | 6
 | 1 | Top.stl | 3D print | 6
 | 8 | Heat Insert | Fastener | 6
 | 4 | M3x16 SHCS | Fastener | 36
 | 4 | Heat Insert | Fastener | 24
 | 2 | M3x50 SHCS | Fastener | 24
 | 2 | M3x20 SHCS | Fastener | 0
 | 1 | Stealthburner Back.stl | 3D print | 0
 | 1 | Stealthburner Base.stl | 3D print | 0
 | 1 | Heat Insert | Fastener | 12
 | 2 | M3x10 SHCS | Fastener | 12
 | 1 | NozzleWiper_Sized-Fusion001.stl | 3D print | 8 | (https://www.printables.com/model/1054455-voron-24-nozzle-brush-using-bambu-labs-a1-silicon)
 | 1 | Bambu lab A1 silicone brush |  | 4
 | 2 | M3x8 SHCS | Fastener | 4
 | 2 | M3 T-Nut | Fastener | 8 | Use hammerhead nuts in case you ever need to move it
 | 4 | 6x3mm magnet | Magnet | 8
 | 1 | 350mm_Bucket.stl | 3D print | 0 | (https://www.printables.com/model/490610-nozzle-scrubber-with-a-large-bucket-for-voron-24-3)
Spool holder | 3 | …
Z cable chain | 1 | z_chain_bottom_anchor.stl | 3D print | 1
 | 2 | [a]_z_chain_retainer_bracket_x2.stl | 3D print | 1
 | 1 | M5x10 BHCS | Fastener | 4
 | 1 | M5 T-Nut | Fastener | 4
 | 2 | M3x10 FHCS | Fastener | 4
 | 1 | Cable chain | Wiring | 1
Sexball probe
 | 1 | HartK probe | PCB | 0
 | 1 | Ball with M5 threads | Fastener | 0
 | 1 | M5x30 pin external thread | Fastener | 1
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

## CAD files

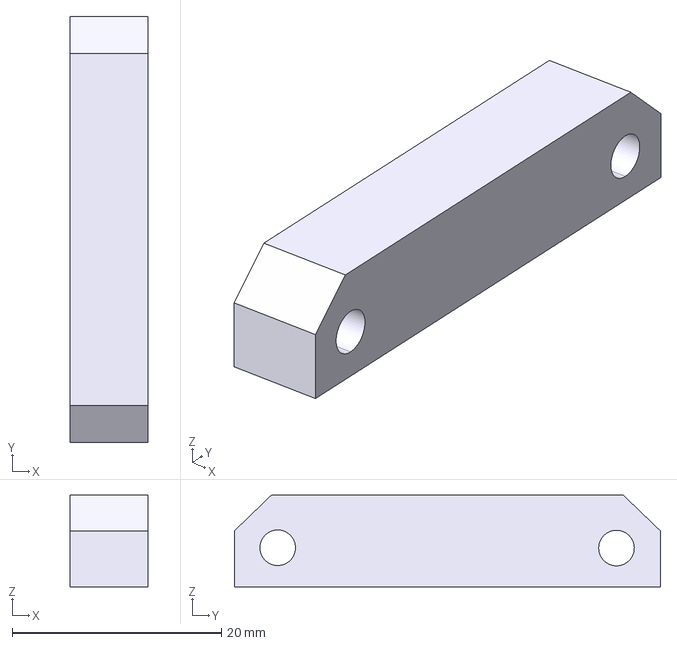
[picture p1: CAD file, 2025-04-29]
CAD/dragknife_stealthchanger_spacer.step
7.50 x 40.7 x 8.75 mm

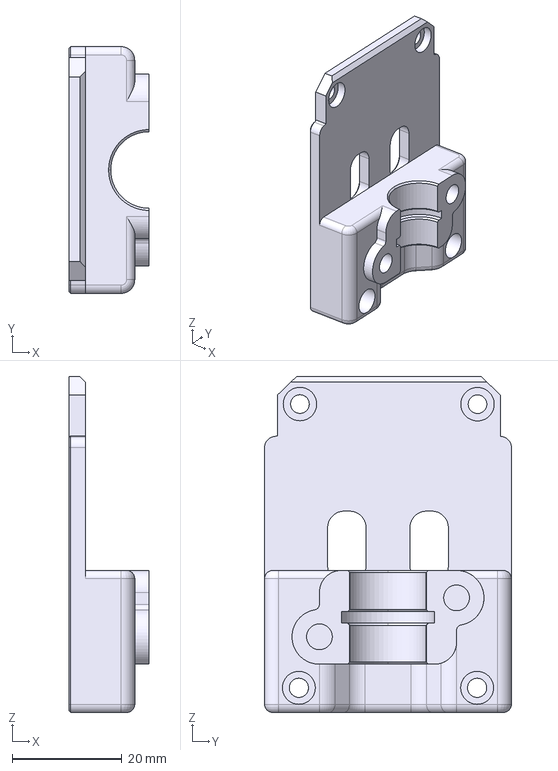
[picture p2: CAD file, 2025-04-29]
CAD/dragknife_stealthchanger_tap.step
14.6 x 45.0 x 61.3 mm

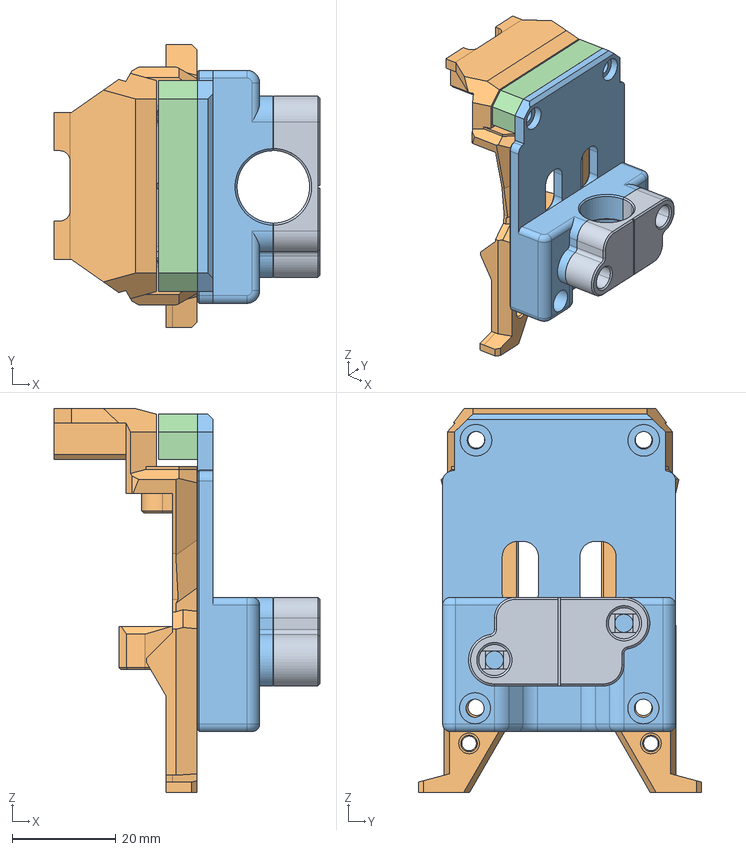
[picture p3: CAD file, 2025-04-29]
CAD/dragknife_sc_sbbackplate.FCStd
51.3 x 54.7 x 74.1 mm
Drag Knife Slider Front
Slice.0 x 2
Slice.1 x 2

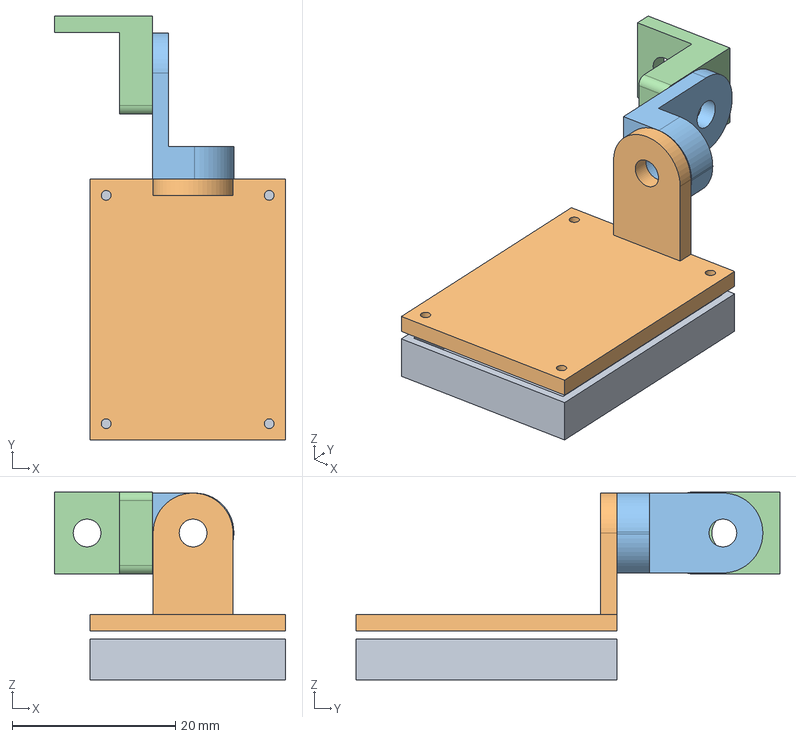
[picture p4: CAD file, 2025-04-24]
CAD/CameraMount.step
28.3 x 52.0 x 23.0 mm

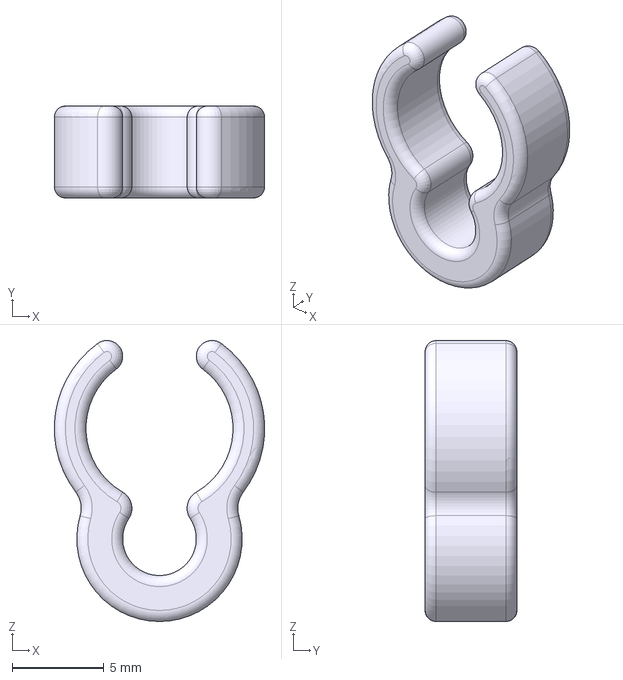
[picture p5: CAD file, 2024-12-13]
CAD/CableClip-Body001.step
11.4 x 5.00 x 15.3 mm

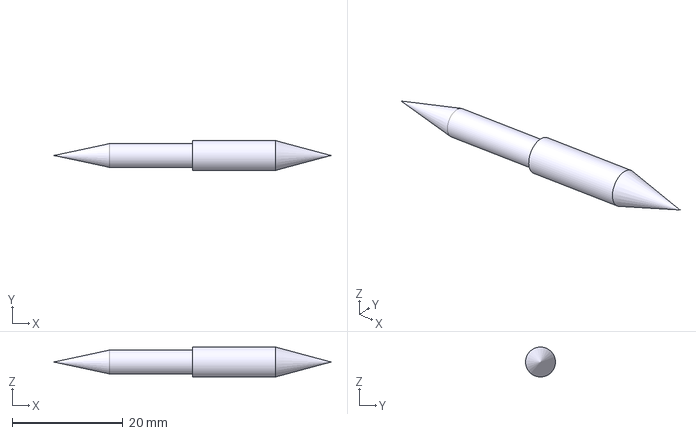
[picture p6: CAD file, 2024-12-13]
CAD/dowelpin.step
50.0 x 5.40 x 5.39 mm

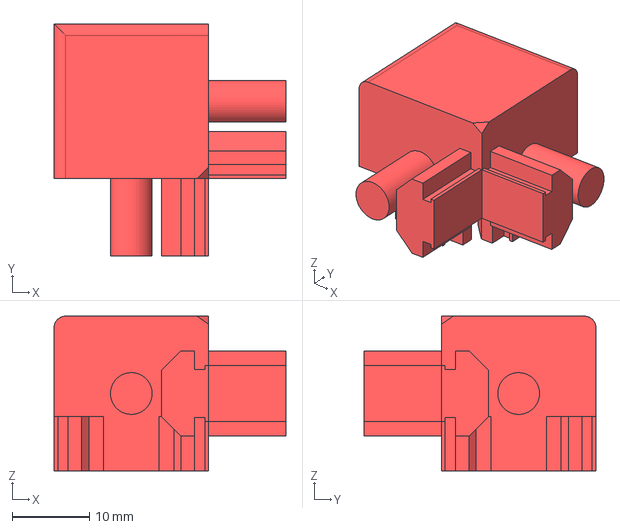
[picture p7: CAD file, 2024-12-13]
CAD/TopHatSpacer_v2.step
30.0 x 30.0 x 20.0 mm

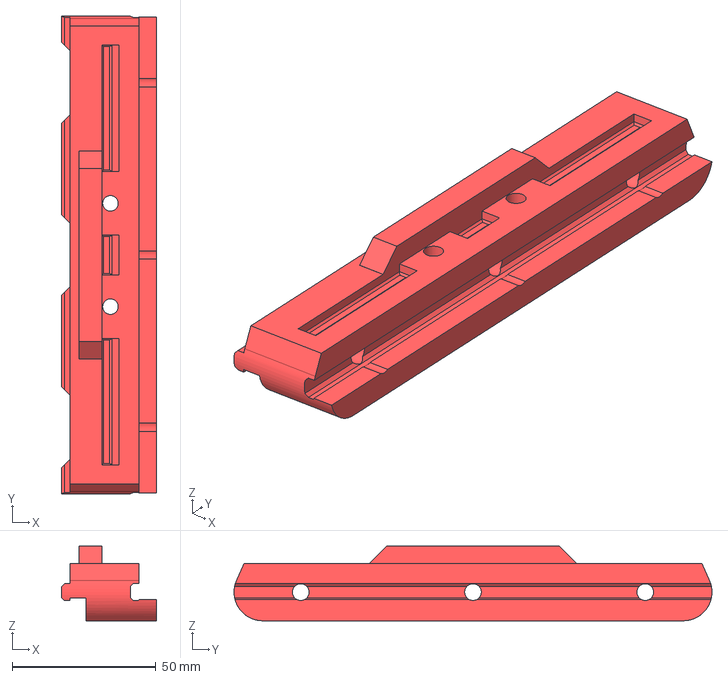
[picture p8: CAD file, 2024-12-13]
CAD/Voron-1-R-Handle-Spacer.step
33.0 x 166.5 x 26.0 mm

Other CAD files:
CAD/CableClip.FCStd
CAD/TopHatSpacer_removedinner.FCStd
CAD/CameraMount.FCStd
CAD/Voron-1-R-Handle-Spacer.3mf
CAD/Voron-1-R-Handle-Spacer.stl
CAD/dowelpin.FCStd

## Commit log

2024-12-13 more stuff, BOM
    [BOM.xlsx, CableClip-Body001.step, CableClip.FCStd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]
2025-04-24 Camera mount
    [CameraMount.FCStd, CameraMount.step]
2026-03-14 Update some outdated things from the readme
    Updated links and descriptions for N3MI exhaust panel and CAN cable distribution.
2026-03-14 Update README with enhancements and clarifications
    Corrected punctuation and added details about toolheads and power supply.
2026-05-03 Add warning about using cheap USB hubs and cables
    Added advice on avoiding cheap USB hubs and cables to prevent communication issues.
2026-05-03 Document filament feeders and communication debugging
    Added detailed notes on filament feeders and debugging communication issues with the 3D printer, including insights on cable management and USB connections.
2026-05-03 Revise README with new image and filament feeder info
    Updated image link and added new filament feeder details.
